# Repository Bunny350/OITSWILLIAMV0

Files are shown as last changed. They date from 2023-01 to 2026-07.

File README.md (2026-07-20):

<p align=center>
    <a>
        <picture>
  <source media="(prefers-color-scheme: dark)" srcset="https://raw.githubusercontent.com/Bunny350/OITSWILLIAMV0/master/Media/Logos/logo-whitetext.svg">
  <source media="(prefers-color-scheme: light)" srcset="https://raw.githubusercontent.com/Bunny350/OITSWILLIAMV0/master/Media/Logos/logo.svg">
  OITSWILLIAMV0
</picture>
    </a>
</p>
Project is being constantly updated. 

# OITSWILLIAMV0

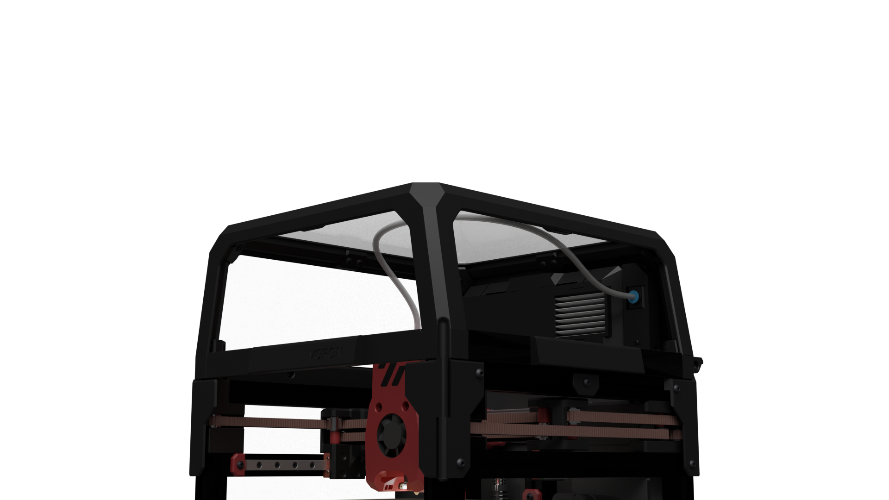
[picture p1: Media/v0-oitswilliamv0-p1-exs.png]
V0.2 + OITSWILLIAMV0 mod


Mod Repository for Voron 0.2

* Currently featured in V0.2378[^config-on-other-side]!

OITSWILLIAMV0 is a mod project for [Voron Zero](https://github.com/VoronDesign/Voron-0) 3D printer after OitswilliamV2. It comes with two different skirt themes, extended skirts and keeps some stock elements.

This mod project goes different, it is to redefine usability without making it look completely different.

## Feature development status
| Feature | Status |
| --- | --- |
| Extended skirt | Released |
| As-is top hat  | Released |
| Exhaust XS | Released |
| Back skirt with ThinkBook 14s fans | Experimental, early access |

## Extended skirt
OITSWILLIAMV0's main feature is the extended skirt, which adds additional 16mm not just to fit 40mm fans to cool down electronics. In front, left and right sides, it uses Trident skirts that are not scaled down, but cut down.

### Variant with ThinkBook 14s fans mounting
This variant is the way where we make 3D printers sound different. This replaces the original's 3510 axial fans.

## As-is top hat
OITSWILLIAMV0 also contains a mod that is used to reduce waste by keeping V0.1 top hat while adding the Cam locks that are introduced for V0.2 extrusion top hat. This mod adds 15mm spacing just for hinges, is made to not use heat seat inserts and can be printed on V0's limited build volume.

## Exhaust XS
Exhaust XS is a *different* type of exhaust unit made for Voron 0. It is intended to be different in sound and the way it is used. The filter cartridge is reusable and can be built & maintained with no tools. 

## BOM requirements and replacements

### Optional (requires extended skirt)
| Stock V0  | V0 with this mod |
| --- | --- |
| NEMA17 Stepper Motor (34mm max) with integrated lead screw 200mm T8x8 | NEMA17 Stepper Motor (40mm) with integrated lead screw 200mm T8x8* |
* Without extended skirt, this replacement will not fit.

### Additional parts

* [Exhaust XS BOM](https://docs.google.com/spreadsheets/d/1qKHTR9wy5eDcJ8kGZrhbsqijIHyDv_TbETnKIMAwmbk/edit?usp=sharing)
  
* Back skirt (legacy)
    * 1x 4010 axial fan
    * 4x M3x16mm BHCS
    * 4X M3x5x4 heat-set inserts
  
* Back skirt (with ThinkBook fans)
    * 1x ThinkBook 14s cooling fan (big)
    * 6x M2x10mm self-tapping screws

* Extended skirt legs (*dc_usb-c_sbc_exhaust_extended_skirt_middle.stl* + *dc_usb-c_sbc_exhaust_extended_skirt_top.stl*)
    * 4x M3x55mm SHCS / BHCS
    * USB-C power legging
        * 1x ThinkBook 14s cooling fan (small)
        * 3x M2x10mm self-tapping screws
        * *These are not required when using with AC power inlet skirt (power-inlet-extended-skirt.stl).*

* Rosalina Theme front covers
    * Both left and right
    * 4x M3x6mm BHCS

* Extended skirt display
    * 2x M3x12mm BHCS instead of M3x6mm BHCS
    * M3x6mm can be kept if mounting the skirt with no display.

* As-is top hat
    * 16x M2x10mm self-tapping screws
    * 8x M3x6mm BHCS

<details>
  <summary>Total BOM excluding EXS</summary>

* Total (excluding EXS)
    * 2x M3x6mm BHCS
    * 2x (without fan), 4x or 6x M3x12mm BHCS
    * 4x M3x55mm SHCS / BHCS

* Total (V0.2378 Rosalina Theme, without top hat or EXS)
    * 6x M3x6mm BHCS
    * 2x (without fan), 4x or 6x M3x12mm BHCS
    * 4x M3x55mm SHCS / BHCS

* Total (normal, with top hat, excluding EXS)
    * 16x M2x10mm self-tapping screws
    * 10x M3x6mm BHCS
    * 2x (without fan), 4x or 6x M3x12mm BHCS
    * 4x M3x55mm SHCS / BHCS

* Total (V0.2378 Rosalina Theme, with top hat, excluding EXS)
    * 16x M2x10mm self-tapping screws
    * 14x M3x6mm BHCS
    * 2x (without fan), 4x or 6x M3x12mm BHCS
    * 4x M3x55mm SHCS / BHCS
</details>

"But can you compare with the normal V0.2?" Heck yes!

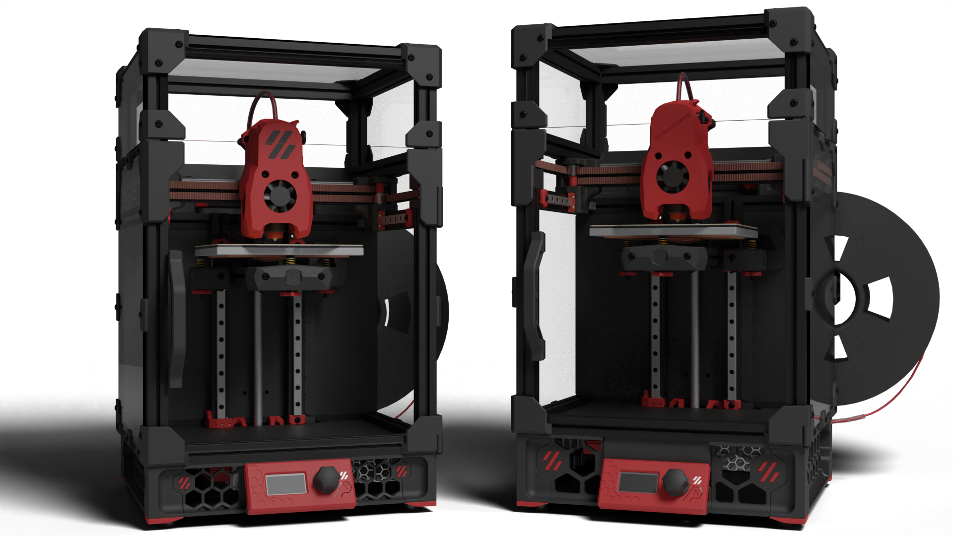
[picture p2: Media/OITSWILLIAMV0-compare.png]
Stock Voron 0.2 and Voron 0.2 with OITSWILLIAMV0 mod

As you can see, the righthand is Voron 0.2 with OITSWILLIAMV0 mod. it has the bigger Voron logo and is taller, which indicates that it uses extended skirt, which allows fit of bigger Z-axis motor. Another thing that it is different is that I modified Mini Stealthburner to reflect my mod. It is just a cosmetic mod but still Voron Mini Stealthburner.

[^config-on-other-side]: The configuration files for the following printers are not included in this repository, only organized, specific and cleaned-up. To get V0.2378's exact configuration files, you must be a follower of Oitswilliam Pang and then get follower-exclusive features through [this form](https://docs.google.com/forms/d/e/1FAIpQLSe9aEM7jyf0lV2PUAgOg0_tz9F7GI91byWFxUzvXsLlXambJA/viewform?usp=header). Other steps are provided from the form.

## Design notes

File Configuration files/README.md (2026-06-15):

# Configuration files
This folder contains mostly Klipper configuration files.

## Guide
* fn_key.cfg
    * A configuration file made specifically to replace *kill_switch* inside *[display]* section. If the key in-question has wired directly to the reset key of MCU then this will be useless.
    * Default functions are provided.
* exs.cfg
    * A dedicated configuration file made for Exhaust XS.

## Other notes
* Only followers of Oitswilliam Pang from Facebook, Instagram and subscribers on YouTube can view and borrow Oitswilliam's printers' (V0.2378) current configurations. This folder holds cleaned-up configurations.

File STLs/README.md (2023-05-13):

This folder stores STLS of this project.
## Compatibility
All mods contained in this project only support Voron Zero 3D printer and some may support 3D printers that use 1515 extrusion as frames.

## Color guide
* [acc] - Printer accent color.
* [base] - Printer base color.
* [transparent] - Transparent color, it should allow the glow to pass-through and can be diffused. Transparent PETG is recommended.
* [rc] - Rosalina Cyan; the best matching color for Oitswilliam's is Polymaker PolyLite ABS teal. This only occur in Rosalina-theme parts.
* If the part name does not have any brackets at the beginning you can use the printer's base color or better use the least used filament to print the part. These parts are mostly hidden on the outside.

##  Printing guidelines
This section tells how to basically configure print settings.
Some parts require a bigger printer to print.
### Settings
These parts require ABS or PETG to print.
Settings and parameters must be set to the following values:
* Layer height 0.2mm
* Layer width of 1.6mm or 4 layer lines
* Infill density of 40%, but,
    * On LED diffusers ([transparent]led-diffuser), the recommended infill density is 100%,
* Any slicers are welcome.
* Some inner parts such as grills requires modifiers to optimize printing performance.

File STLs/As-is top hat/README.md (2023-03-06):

This folder contains essential components of As-is top hat mod.

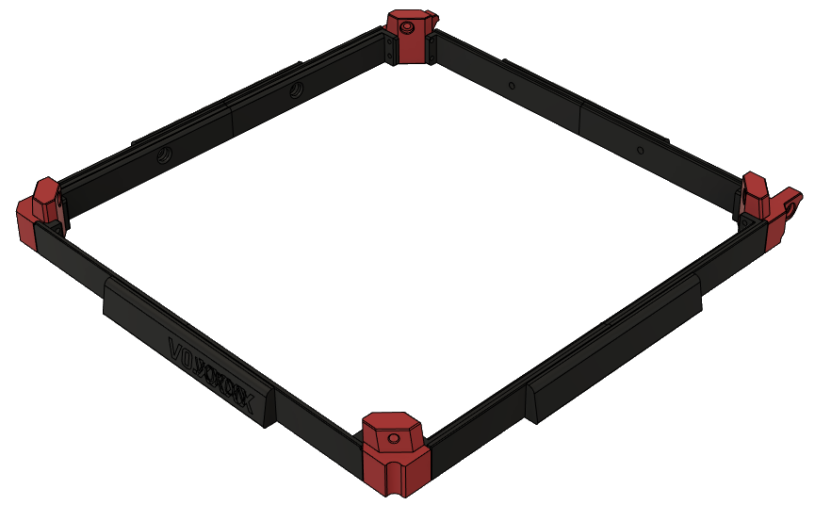
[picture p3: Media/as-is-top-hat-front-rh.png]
As-is top hat mod front-right

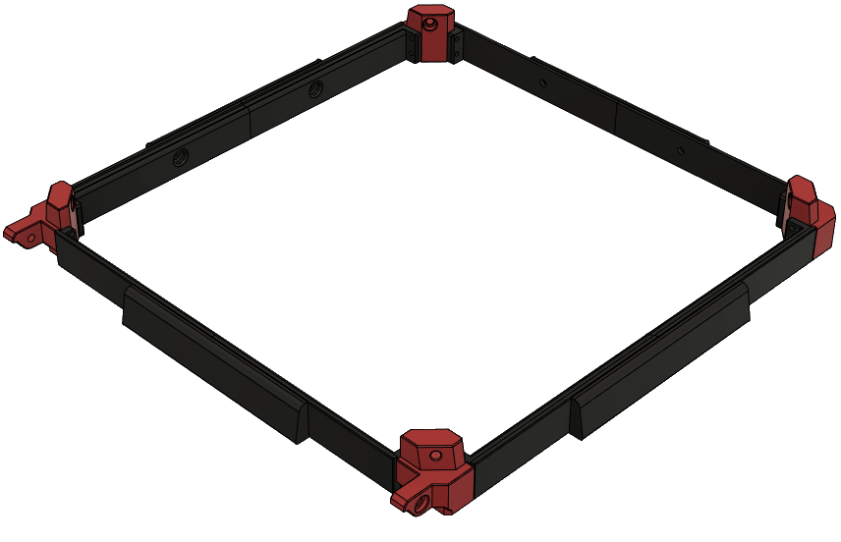
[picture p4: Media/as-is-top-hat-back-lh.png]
As-is top hat mod back-left


## Printing guide

You may print all the parts in this folder, but not this folder's subfolders, in which you may print either one of the versions of side panels, normal, thick or ultra-thick.

### Side panels foam taping
There are requirements in which the thickness the foam tape is needed.
* Thick version requires at least 3mm thick foam tapes.
* Ultra-thick version does not require any foam tapes in the side. It is optional.

## Assembling As-is top hat

Oitswilliam Pang made a simple design that makes the top hat mod assembly easy, these mount covers are directional, and they need to be faced. Front and back has mount offsets, while the side spacing brackets are thicker.

Re-printing V0.1 top hat is not required, if you have one that isn't been disassembled or salvaged.

Before attaching the corners, they need to be assembled as a ring or halo.

If you want the cam lock feature with this mod, you can attach M3x10mm screws to the bottom hole of the front corners. In V0.2 assembly guide page 232, the screws needs to be spaced and is fixed at 5mm.

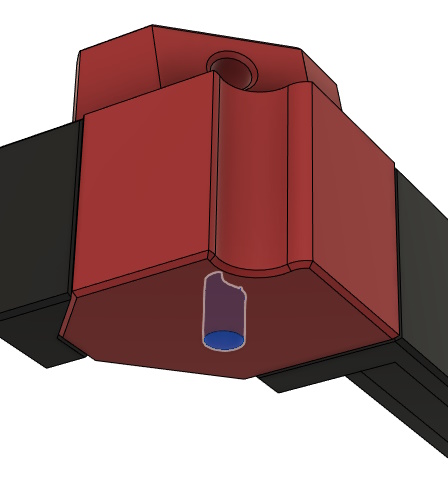
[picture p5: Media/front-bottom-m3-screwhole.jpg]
M3x10mm Cam lock mounting screw hole in one of the corners


To assemble the ring or halo, you attach the spacing brackets to the corners, and secure it with 2 M2x10mm self-tapping screws on each corner, or 4 on each side / corners (16 total). 

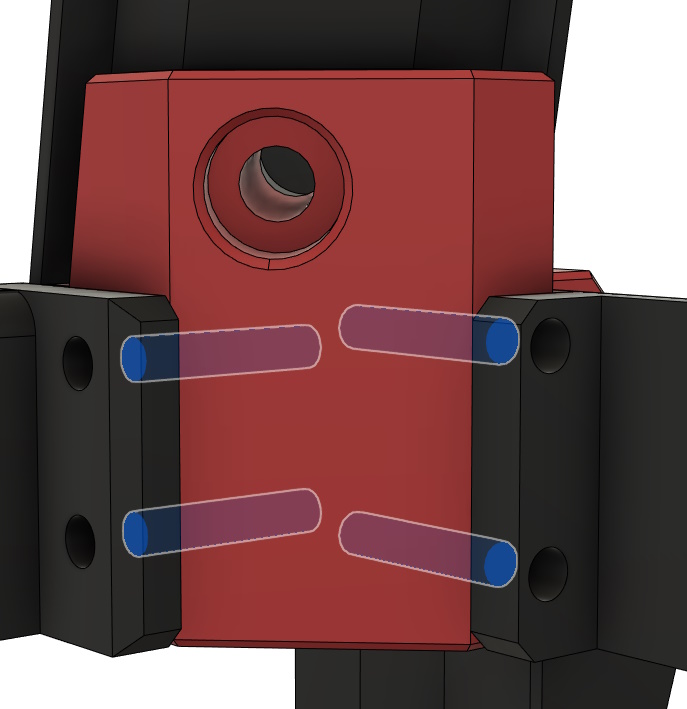
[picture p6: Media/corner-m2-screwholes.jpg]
Mounting holes for attaching M2x10mm self-tapping screws to one of the corners


Then you combine the spacing brackets first, by mounting them with *spacer-holder*, and secure with 2 M3x6mm screws per side (8 total).

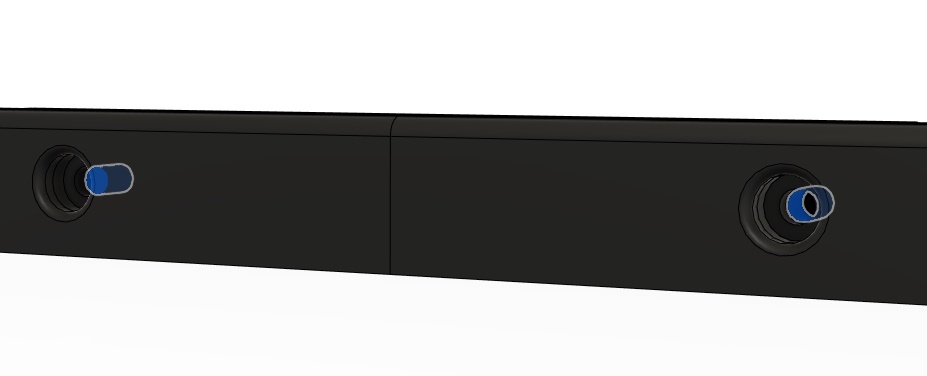
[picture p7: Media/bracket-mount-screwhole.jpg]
M3x6mm to spacer-holder screw mount holes


This is then you can attach the ring or halo assembly that has corners with M3x12 screws in V0.1 assembly manual, and you may follow the rest in V0.2 assembly manual, most specifically back to page 238.

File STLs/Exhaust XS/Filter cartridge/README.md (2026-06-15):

## Known issues
* In some cases Klipper has an issue where it causes an error on moves out of range. Especially on V0 printers with input shaping tuned and enabled.
    * This is not the slicer-side issue, but rather the printer-side issue.
    * To address this, off-center exs_v0_filter_cartridge_carbon_pellet.stl slightly left around 0.4mm in the slicer.

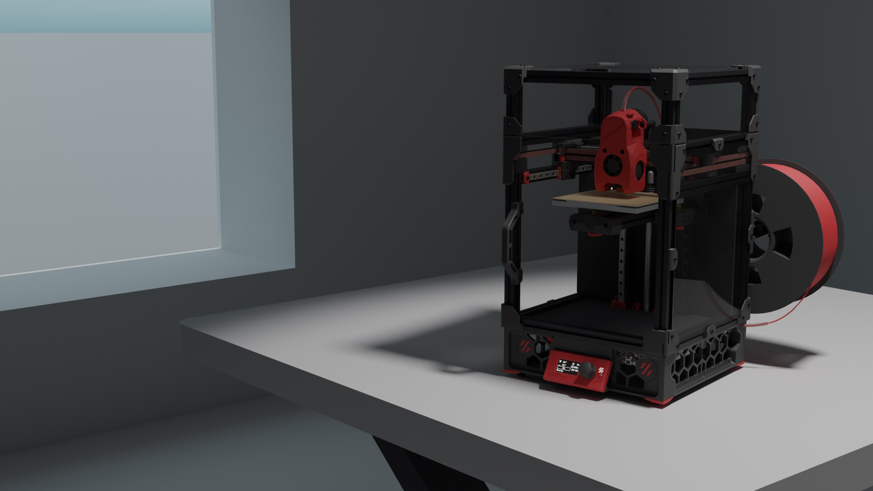
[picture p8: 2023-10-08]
Media/v0-oitswilliamv0-p1-finale.jpg

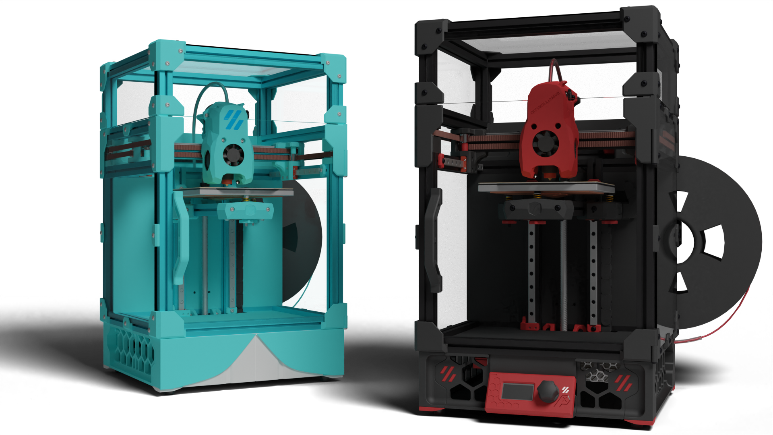
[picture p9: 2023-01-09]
Media/Past renders/OITSWILLIAMV0.png

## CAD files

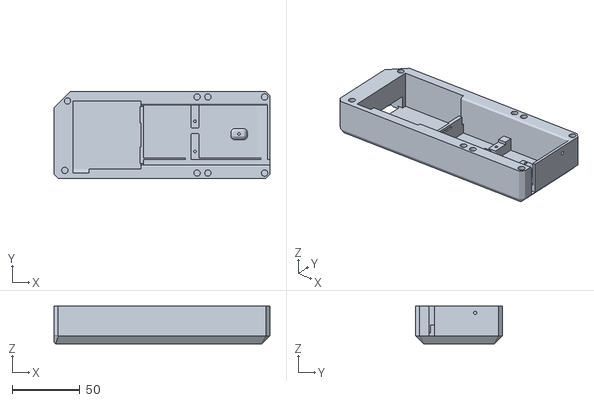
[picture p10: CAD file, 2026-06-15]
STLs/Exhaust XS/Filter mount/Main full/exs_v0_filter_main_unit_bottom.stl
160.0 x 64.4 x 28.0

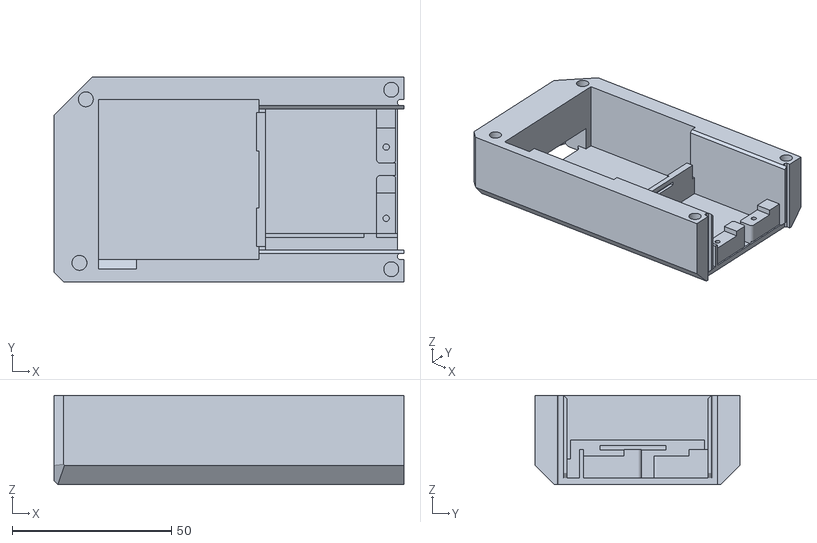
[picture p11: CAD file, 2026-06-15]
STLs/Exhaust XS/Filter mount/Main splitted/exs_v0_filter_main_unit_bottom_split_l.stl
110.0 x 64.4 x 28.0

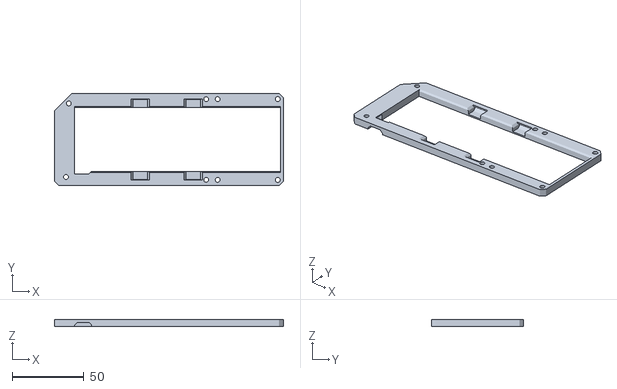
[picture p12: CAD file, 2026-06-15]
STLs/Exhaust XS/Filter mount/Main full/exs_v0_filter_main_unit_top.stl
160.0 x 64.4 x 5.00

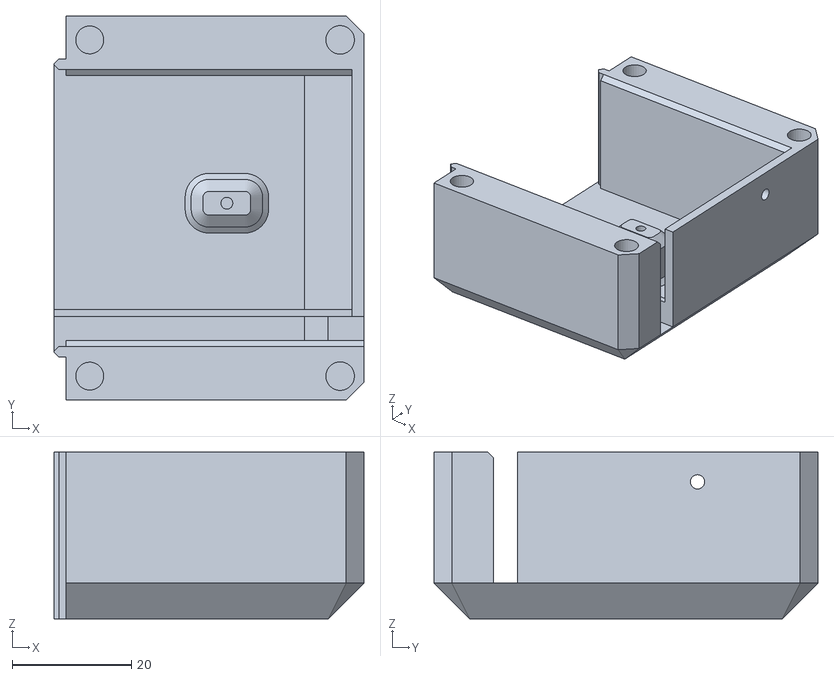
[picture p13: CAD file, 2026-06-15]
STLs/Exhaust XS/Filter mount/Main splitted/exs_v0_filter_main_unit_bottom_split_r.stl
52.0 x 64.4 x 28.0

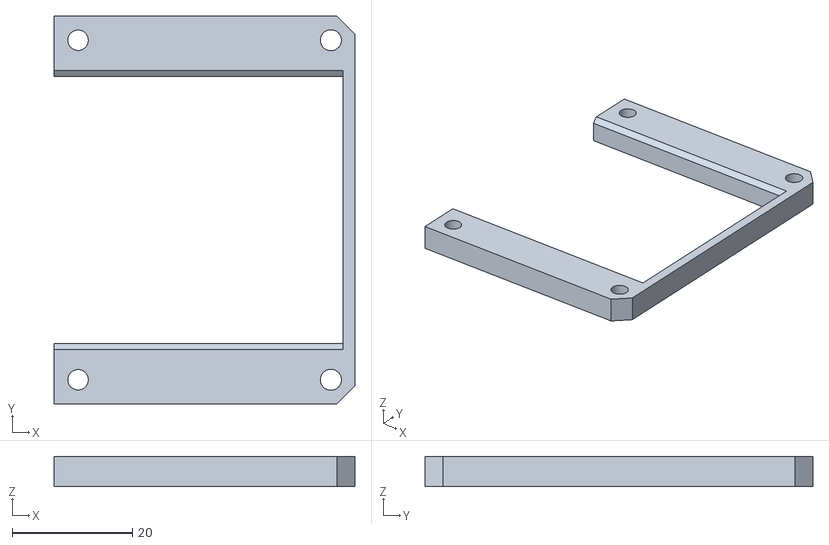
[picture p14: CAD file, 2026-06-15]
STLs/Exhaust XS/Filter mount/Main splitted/exs_v0_filter_main_unit_top_split_r.stl
50.0 x 64.4 x 5.00

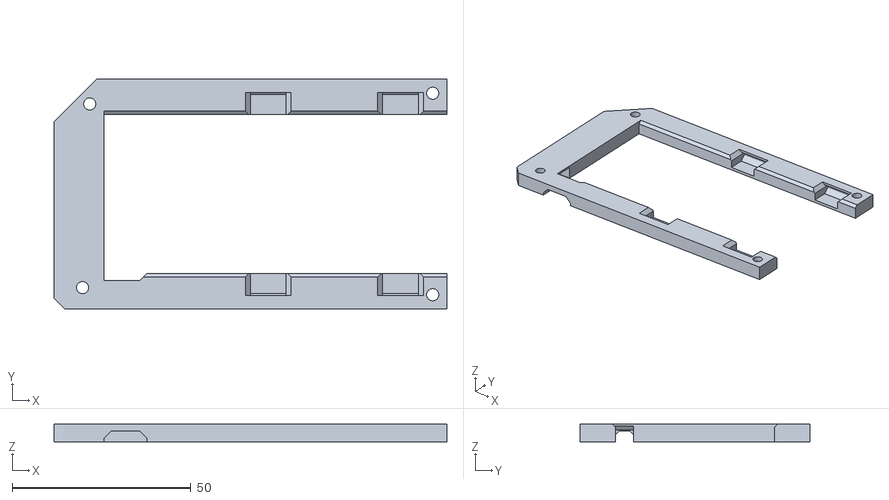
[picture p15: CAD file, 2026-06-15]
STLs/Exhaust XS/Filter mount/Main splitted/exs_v0_filter_main_unit_top_split_l.stl
110.0 x 64.4 x 5.00

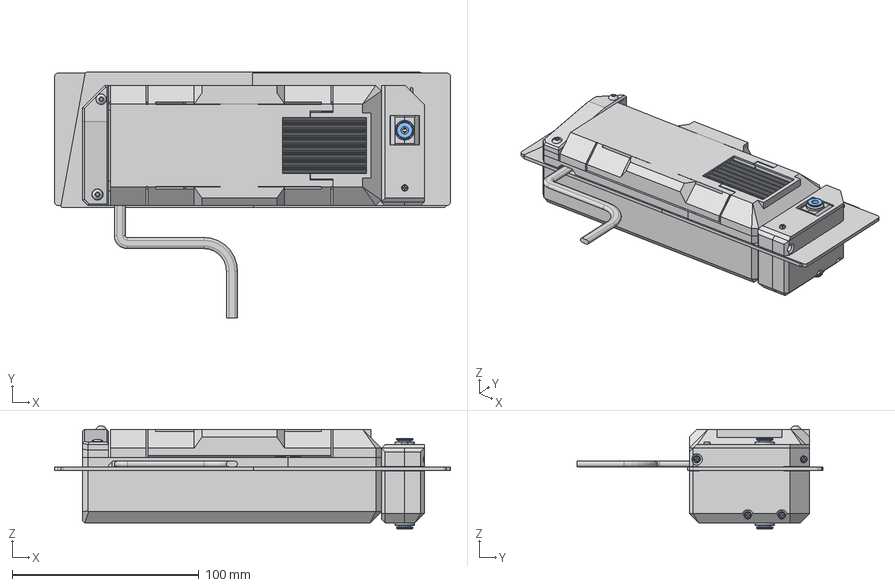
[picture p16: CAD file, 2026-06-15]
CAD/Exhaust XS/EXS for voron 0.step
212.0 x 131.4 x 54.9 mm
[raw] hepa filters
filter cartridge
99461A917_NO THREADS_Phillips Rounded Head Thread-Forming Screws x 13
KW10 Microswitch (2)
10x20x0.7 stainless steel spring - compressed
Omron D2F Microswitch
4mm OD 2mm ID PTFE tube
MR85 Bearing x 2
led mount
[raw]babydrone back led
v0.1 panel
v0.2 panel
main unit splitted
92095A182_NO THREADS_Button Head Hex Drive Screw x 8
ISO 7380-1 - M3 x 30 Steel 4.6 Plain
ISO 7380-1 - M3 x 30 Steel 4.6 Plain_1
M3 Threaded Insert x 8
ECAS04 Bowden Collet x 2
raw - 5010 blower fan
raw - cabling - for reference only
raw - foam tape

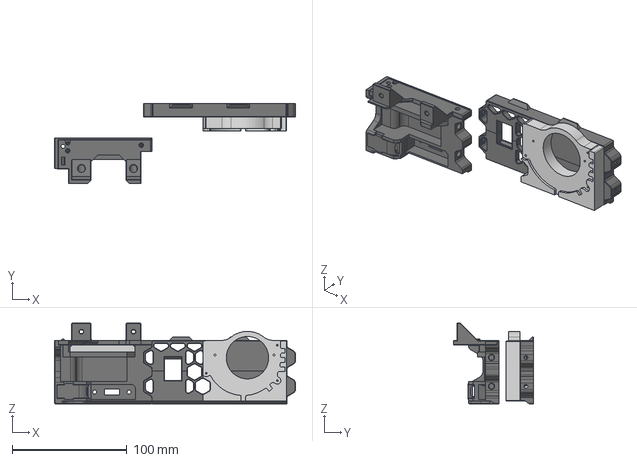
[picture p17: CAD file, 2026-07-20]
CAD/Experimental/voron 0 skirt with laptop fan mod.step
210.5 x 70.0 x 70.5 mm

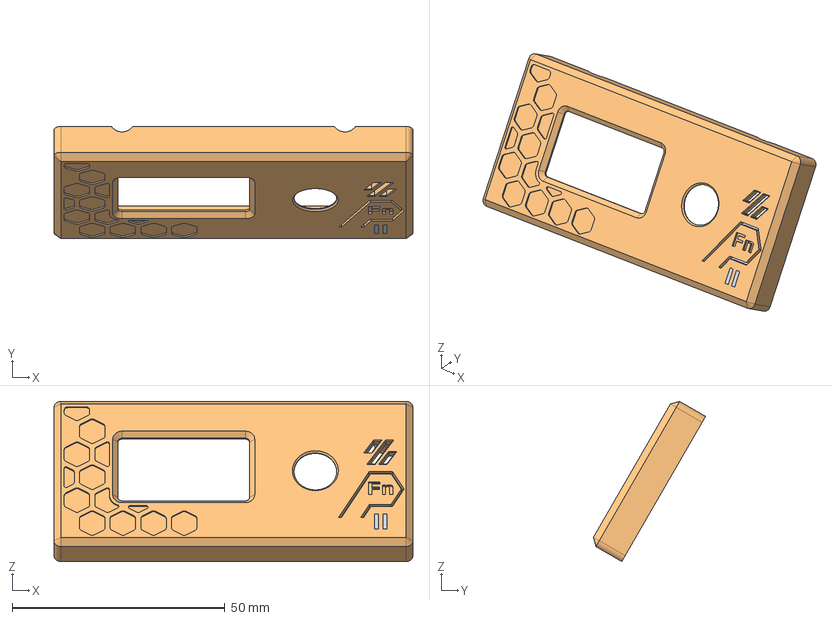
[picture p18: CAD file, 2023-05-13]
CAD/Faceplates with Function key/voron 0.2 display front faceplate with fn button v2.step
84.4 x 26.4 x 37.6 mm

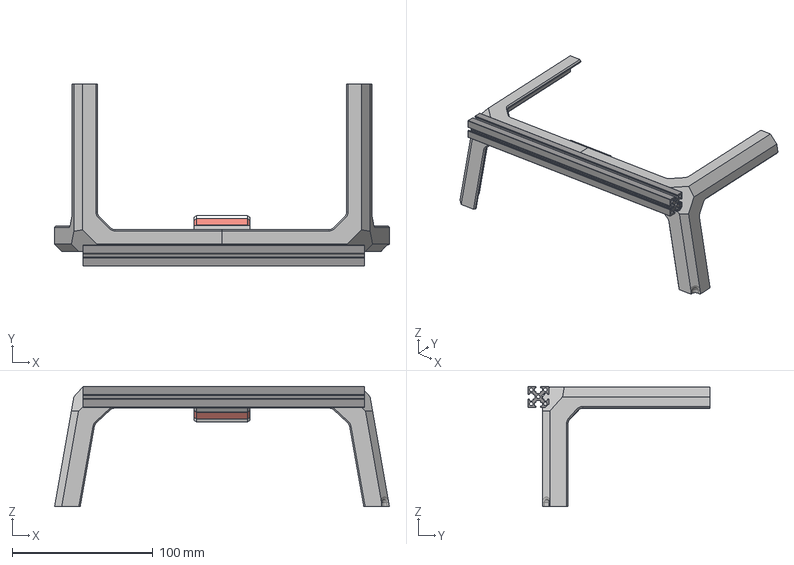
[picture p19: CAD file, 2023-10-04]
CAD/Top hat LED/v0 led addon v4.step
238.0 x 129.6 x 85.5 mm
M3x8 BHCS-1 x 3
original parts
M3 Hexnut
original parts (1)
frame side magnet
M2x10 Self-tapping Screw (2) x 4
WS2812B LED v1 x 2
led side magnet
wire

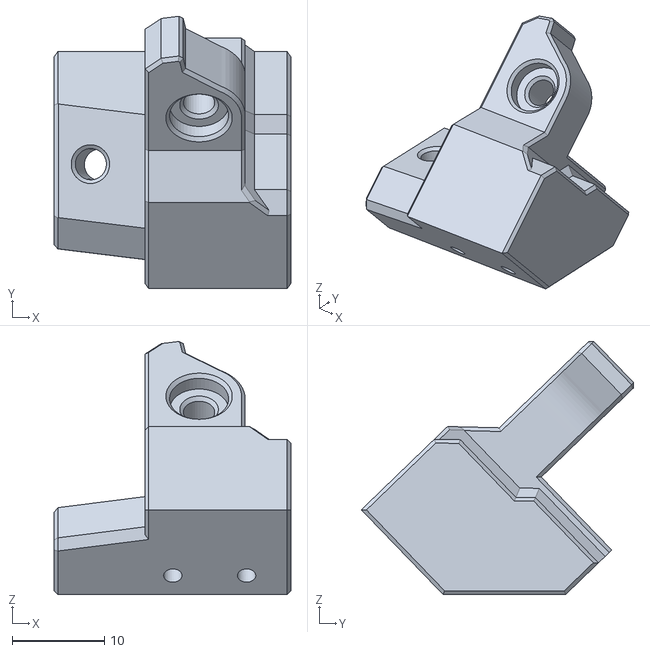
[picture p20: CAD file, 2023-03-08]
STLs/As-is top hat/corner-hinge-left.stl
25.6 x 29.5 x 27.4

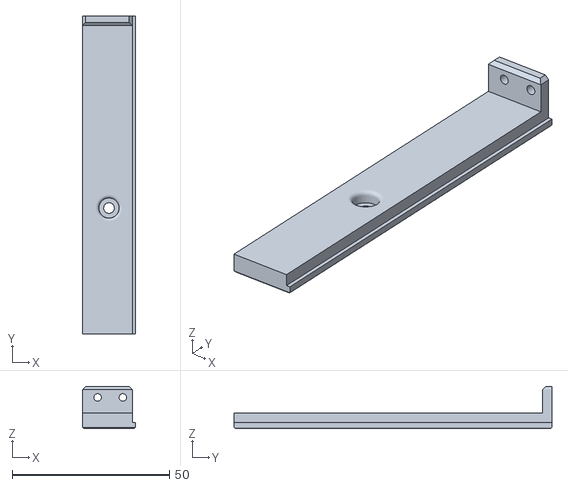
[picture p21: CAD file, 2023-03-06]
STLs/As-is top hat/Thick/spacer-side-thick-mirror-X2.stl
16.8 x 101.0 x 13.4

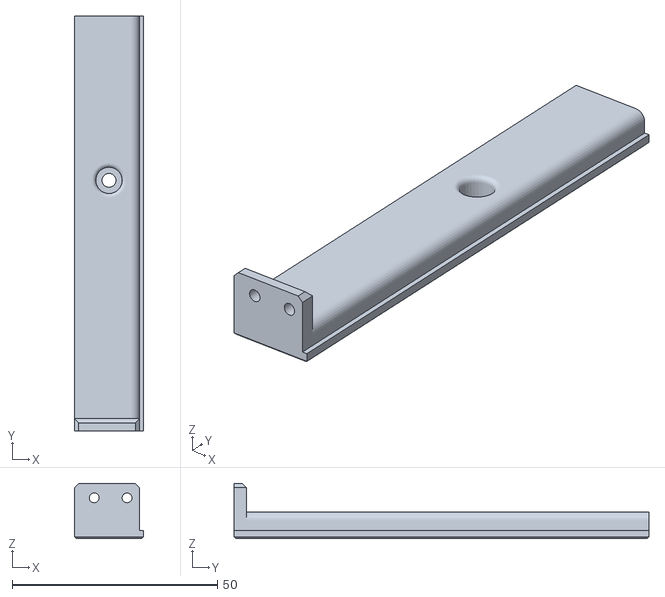
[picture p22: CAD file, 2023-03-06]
STLs/As-is top hat/Ultra-thick/spacer-side-ultra-thick-X2.stl
16.8 x 101.0 x 13.4

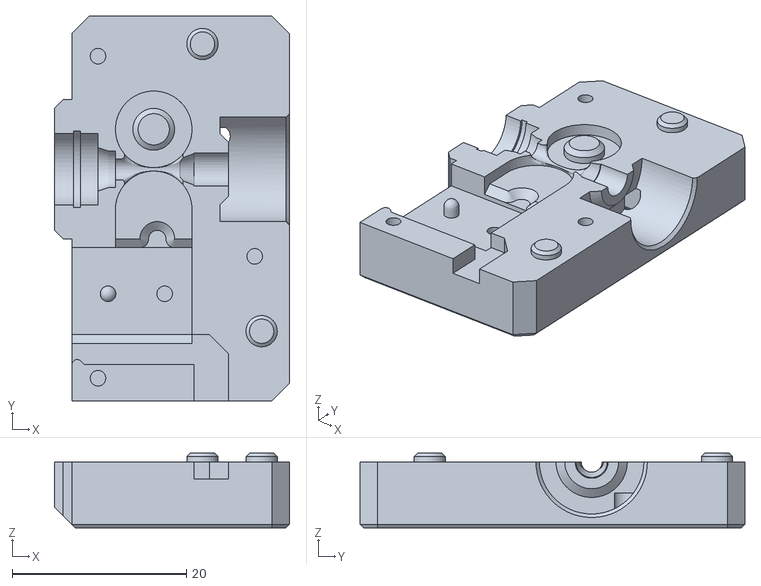
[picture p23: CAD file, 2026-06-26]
STLs/Exhaust XS/Filament sensor/exs_presence_tangle_pres_l.stl
27.0 x 44.2 x 8.60

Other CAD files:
STLs/Exhaust XS/Filter cartridge/exs_v0_filter_cartridge_front_bracket.stl
STLs/Exhaust XS/Filter mount/exs_v0_filter_reserved.stl
STLs/Exhaust XS/LED unit/exs_led_unit_shell.stl
STLs/Exhaust XS/Unit panel mount/V0.1 (printed top-hat)/filter_mount_panel_v0-1_l.stl
CAD/Exhaust XS/EXS for voron 0.f3d
CAD/Experimental/voron 0 skirt with laptop fan mod.f3d
CAD/Faceplates with Function key/voron 0.2 display front faceplate with fn button v2.f3d
CAD/Rest of assembly/OITSWILIAMV0 P1 V0.2.f3d
CAD/Top hat LED/v0 led addon v4.f3d
STLs/As-is top hat/Thick/spacer-side-thick-X2.stl
STLs/As-is top hat/Ultra-thick/spacer-side-ultra-thick-mirror-X2.stl
STLs/As-is top hat/corner-front-left.stl
STLs/As-is top hat/corner-front-right.stl
STLs/As-is top hat/corner-hinge-right.stl
STLs/As-is top hat/spacer-front-lefthand.stl
STLs/As-is top hat/spacer-front-righthand.stl
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

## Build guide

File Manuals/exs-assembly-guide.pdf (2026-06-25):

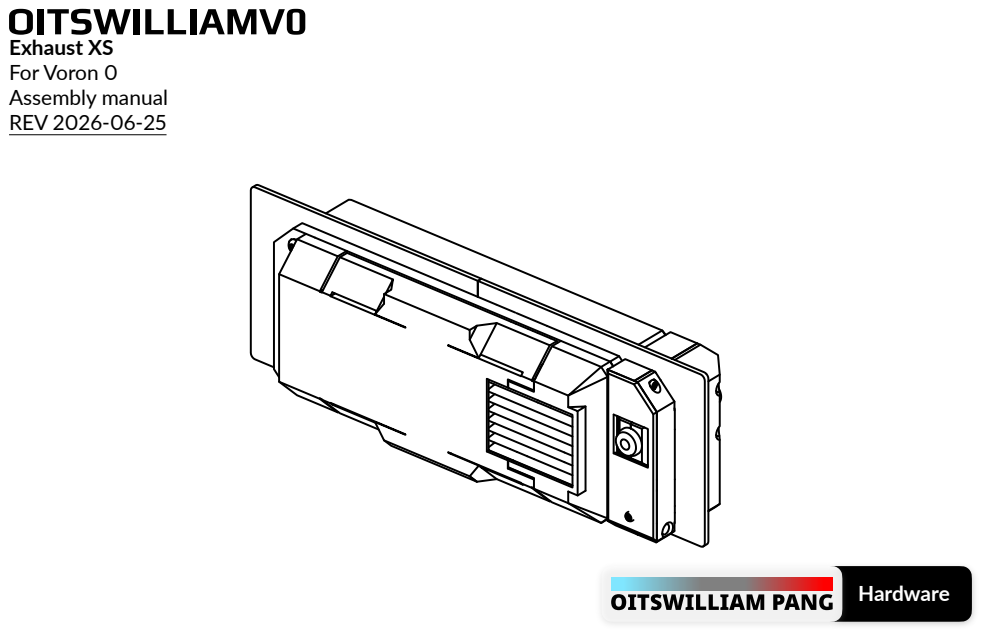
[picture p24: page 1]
Exhaust XS For Voron 0 Assembly manual REV 2026-06-25; Hardware

2
Contents • Before getting started • Assembly • Filter cartridge • Hybrid filament sensor • The outer side • LED unit • Crafting • Attaching and removal • Software configuration • Troubleshooting

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
# Before getting started

You are about to read the manual of Exhaust XS.
Warning
Danger: unless if it only runs on DC and only has a DC input, otherwise risk of electric shock
- Even though you can build with this mod from start, if you want to wire, or re-wire, you need to make sure and check that the mains is unplugged.
- Failure doing so which is unplugging the mains power may cause electrocution or even death.
- When in doubt, please don't touch the wires connected to the power supply or SSR.
Other notes
- Exhaust XS does not support hose adapters from ELG2 or ELG1.
- There is a reserved component that is [redacted], but we will reveal it within foreseeable future, so stay tuned (https://www.oitswilliam.com/media) by following Oitswilliam Pang in Facebook, Instagram and YouTube.

About Exhaust XS
Exhaust XS (XS stands for eXtra small, abbreviated EXS) is Oitswilliam-designed exhaust unit made for Voron 0. It is low-profile, has dual-layer HEPA filters to filtrate microplastics and activated carbon pellets to capture VOCs. EXS uses 5010 blower fan to make exhausting sound different whilst performant. It partially uses Voron Design's Stealth design scheme. EXS uses compliant design just to reduce raw materials and ease assembly, such as removable pellet panel and tool-less cartridge removal. It will pave for the next generation of EL for standard Voron printers.

Dark lore: The name EXS has been around inside Oitswilliam's brain since around 2024.

4
Compatibility
Exhaust XS is compatible with Voron 0, with pre-made 3D-printable panels made specifically for V0.1 (printed top-hat) and V0.2 (extrusion top-hat). Other printers that are smaller than 40cm in either dimensions and did not have a pre-done exhaust cutout are also applicable. Note that top-hat from Voron 0.0 is incompatible.

Contribution
This project can be contributed through GitHub. You can visit, contribute and report new issues here. (https://github.com/Bunny350/alpha-ea/) Technical support
You can contact Oitswilliam here. (http://oitswilliam.com/support) You can email or direct message Oitswilliam in Facebook. Or if the issue is not related to OITSWILLIAMV0 mod, but rather most of Voron parts, you may visit Voron forum or its Discord server.

Guide and legend

- - raw material
- - highlighted material
- - printed material, as this part is simple, the printed parts may be color-coded.

Material

Model
model.stl / model.3mf

Material

5
Part printing
The parts of this model can be printed in the base color of the printer. Bold text indicates the recommended value and italic text indicates on what setting / value it needs to set. Diffuser part require transparent materials, commonly seen in PETG or PC.

Additional maker tools
To get started building the project, you may use the following tools:
- Wire crimping tool - to make custom-length connectors,
- Soldering iron - to connect the switches with wires,
- Heat shrink tubings, in 2mm diameter, three colors minimum.
FDM / FFF or SLS | Print material: ABS, ASA or PA12, prohibits PLA.
Layer height of 0.2mm, initial layer height can be 0.2mm or higher. | Nozzle and extrusion width must be forced 0.4mm; if using 0.4mm nozzle
1.6mm wall width, or 4 wall counts. | Infill must be at least 40%, except on the infill modifiers.
At least 4 solid bottom and top layers, except on the infill modifiers. | The best print speed is up to 120mm/s. The speed might be reduced by the hot end flow rate.
Supports are recommended for main skirt parts. Use tree or organic supports if available. | Other settings might be depended on your printer. Follow it's warnings for proper handling.

# Assembly

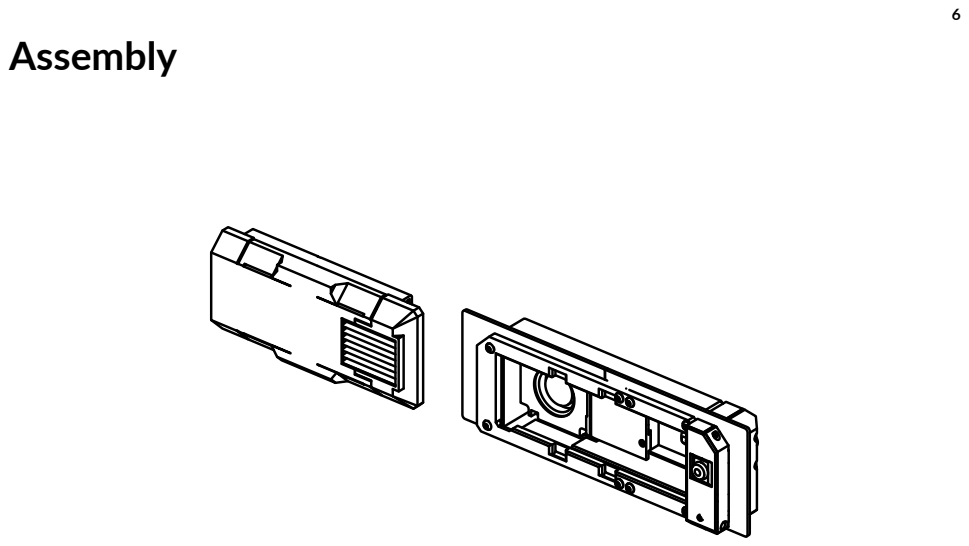
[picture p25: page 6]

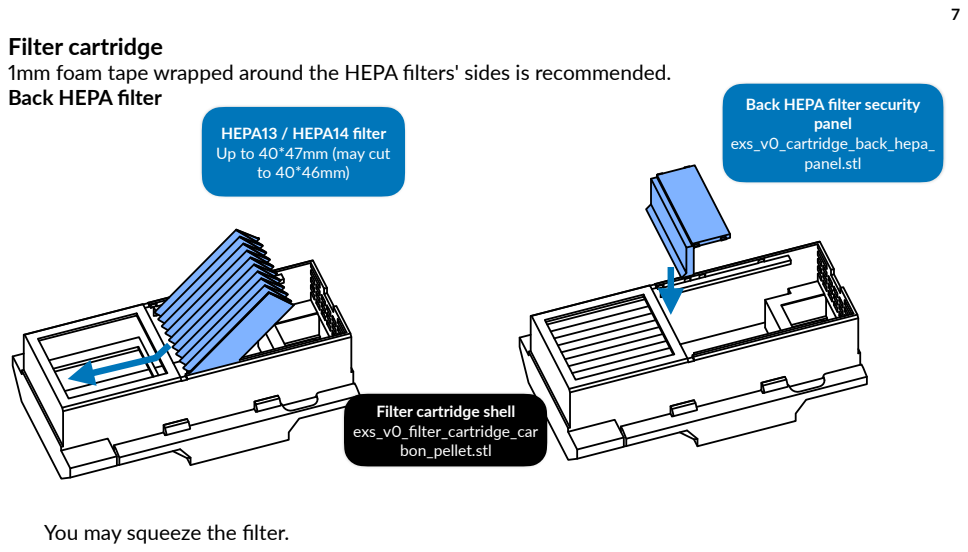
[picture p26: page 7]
Filter cartridge shell exs_v0_filter_cartridge_car bon_pellet.stl; panel exs_v0_cartridge_back_hepa_ panel.stl

Filter cartridge
1mm foam tape wrapped around the HEPA filters' sides is recommended.
Back HEPA filter

Back HEPA filter security

HEPA13 / HEPA14 filter
Up to 40*47mm (may cut

You may squeeze the filter.

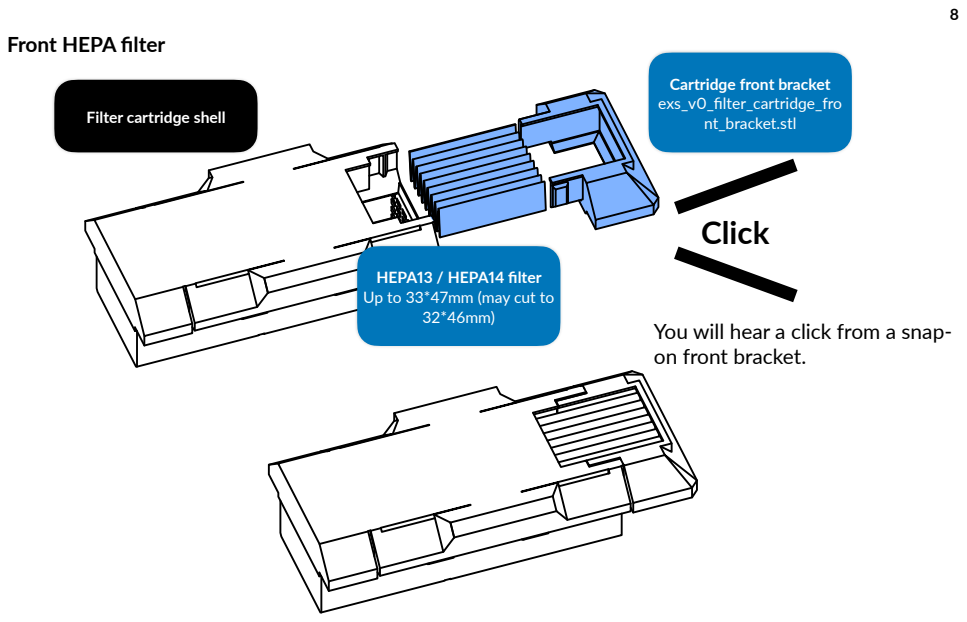
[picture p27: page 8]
Cartridge front bracket exs_v0_filter_cartridge_fro nt_bracket.stl; Click

Front HEPA filter

Filter cartridge shell

HEPA13 / HEPA14 filter
Up to 33*47mm (may cut to

You will hear a click from a snap-
on front bracket.

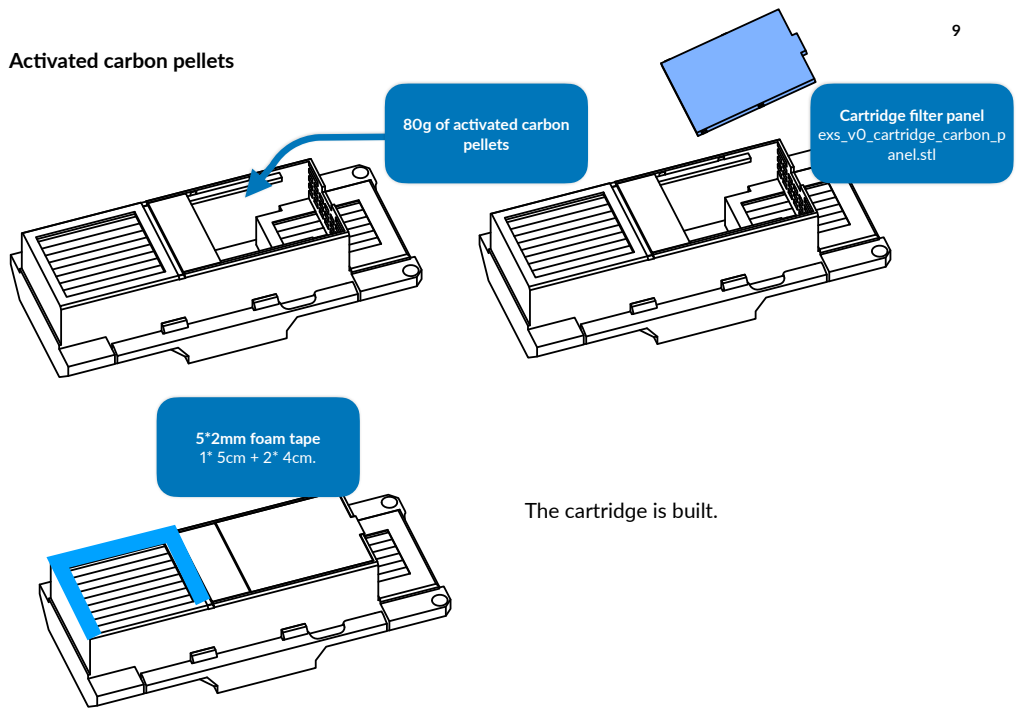
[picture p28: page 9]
pellets; anel.stl; 5*2mm foam tape 1* 5cm + 2* 4cm.

Activated carbon pellets

Cartridge filter panel
exs_v0_cartridge_carbon_p

80g of activated carbon

The cartridge is built.

10
Hybrid filament sensor (presence and tangle sensor)
This is recommended if your Voron 0 did not have any filament run-out and / or tangle sensor. EXS can be installed with or without hybrid filament sensor. This can be ignored if you are installing EXS with Mellow MDM.
Wiring

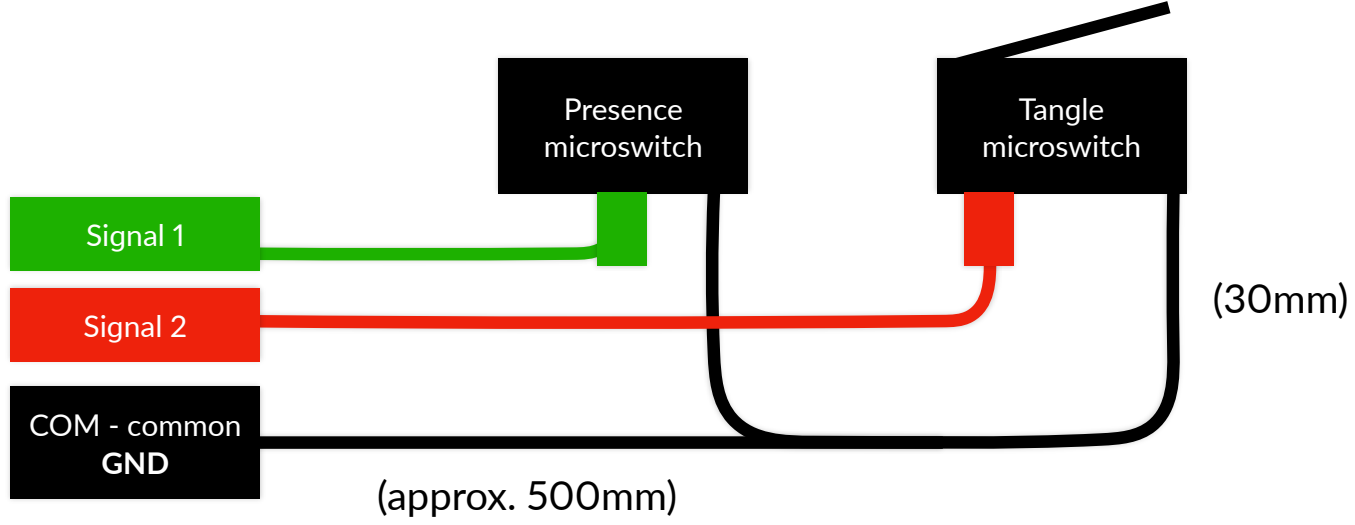
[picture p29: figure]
Presence microswitch; Tangle microswitch; COM - common GND; Signal 1; Signal 2; (approx. 500mm)

Note: it's best time to have two pairs & three colors of heat-shrink tubes for color indication.
Connect the first long signal wire to the normally open (NO) terminal of the presence switch, and then connect the second long signal to the normally closed (NC) terminal of the tangle switch, after that, use the 30mm wire to connect the common (COM) of the switches and use the last long signal wire to the presence switch.

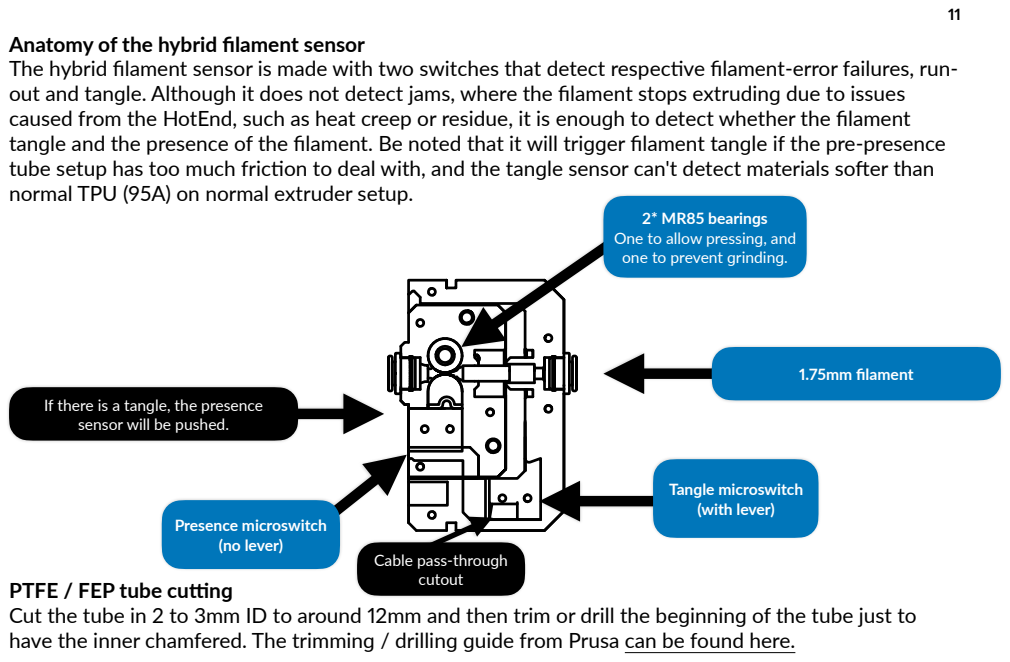
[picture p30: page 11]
1.75mm filament; Presence microswitch (no lever); Tangle microswitch (with lever)

Anatomy of the hybrid filament sensor
The hybrid filament sensor is made with two switches that detect respective filament-error failures, run-
out and tangle. Although it does not detect jams, where the filament stops extruding due to issues
caused from the HotEnd, such as heat creep or residue, it is enough to detect whether the filament
tangle and the presence of the filament. Be noted that it will trigger filament tangle if the pre-presence
tube setup has too much friction to deal with, and the tangle sensor can't detect materials softer than
normal TPU (95A) on normal extruder setup.

2* MR85 bearings
One to allow pressing, and
one to prevent grinding.

If there is a tangle, the presence
sensor will be pushed.

Cable pass-through
cutout

PTFE / FEP tube cutting
Cut the tube in 2 to 3mm ID to around 12mm and then trim or drill the beginning of the tube just to
have the inner chamfered. The trimming / drilling guide from Prusa can be found here. (https://help.prusa3d.com/guide/how-to-trim-ptfe-tube-original-prusa-printers_22424)

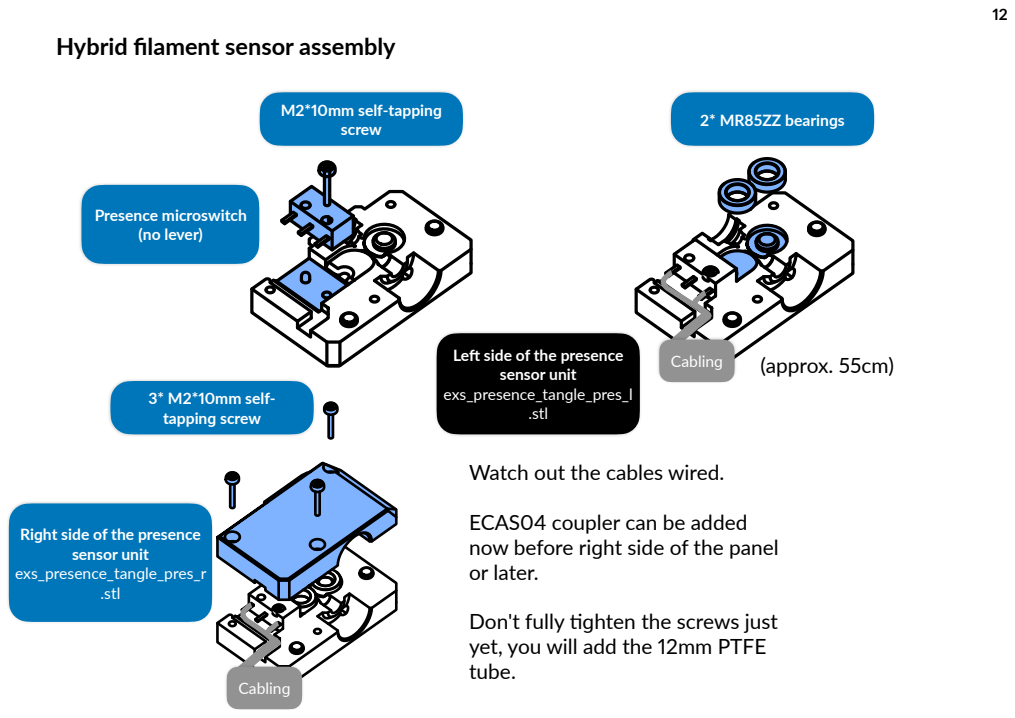
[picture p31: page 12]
Presence microswitch (no lever); M2*10mm self-tapping screw; .stl; 2* MR85ZZ bearings; exs_presence_tangle_pres_r .stl; 3* M2*10mm self- tapping screw; Cabling; (approx. 55cm)

Hybrid filament sensor assembly

Left side of the presence
sensor unit
exs_presence_tangle_pres_l

Watch out the cables wired.

ECAS04 coupler can be added
now before right side of the panel
or later.

Right side of the presence

Don't fully tighten the screws just
yet, you will add the 12mm PTFE
tube.

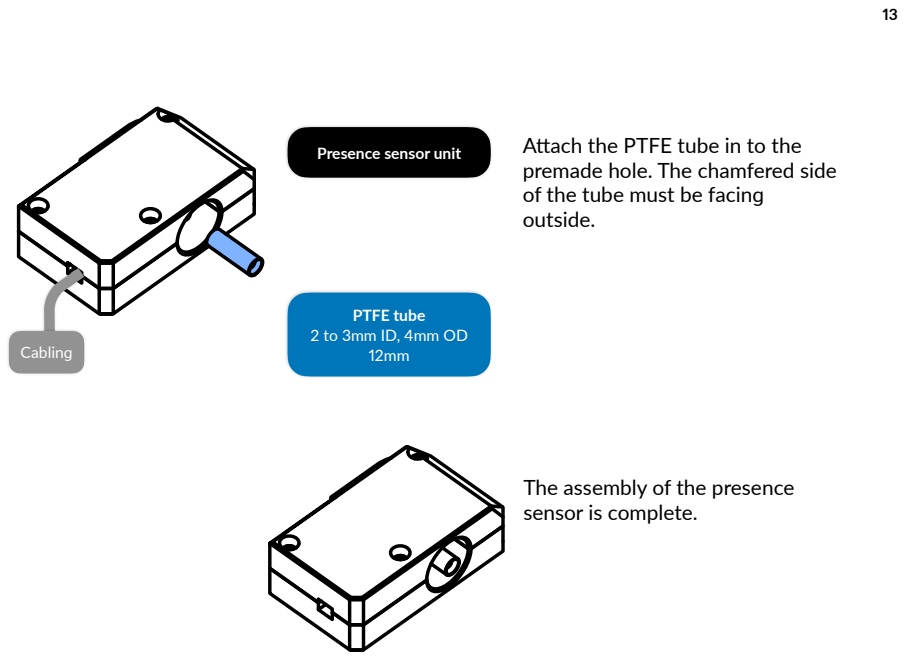
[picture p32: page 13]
Cabling

Attach the PTFE tube in to the
premade hole. The chamfered side
of the tube must be facing
outside.

Presence sensor unit

PTFE tube

The assembly of the presence
sensor is complete.

14
Tangle sensor

Presence sensor unit

M2*10mm self-tapping
screw

10*25*0.7mm stainless
steel spring

Note: watch out for the cables. You may lift the presence sensor up. Note: you may pass the wires through the cutout near the
tangle switch mount.
Test the tangle microswitch by pressing the presence sensor and the shell, you may put the hand at the righthand side of the presence sensor as to prevent component flyaway.
You should hear a click, if not, the switch might be incompatible or the part printed has settings badly tuned. If the problem persists, please flag it as error on GitHub.com/Bunny350/OITSWILLIAMV0/issues.

Left side of the sensor
unit shell
exs_presence_tangle_sh
ell_l.stl

(Cabling approx.
55cm)

Tangle microswitch (with
lever)

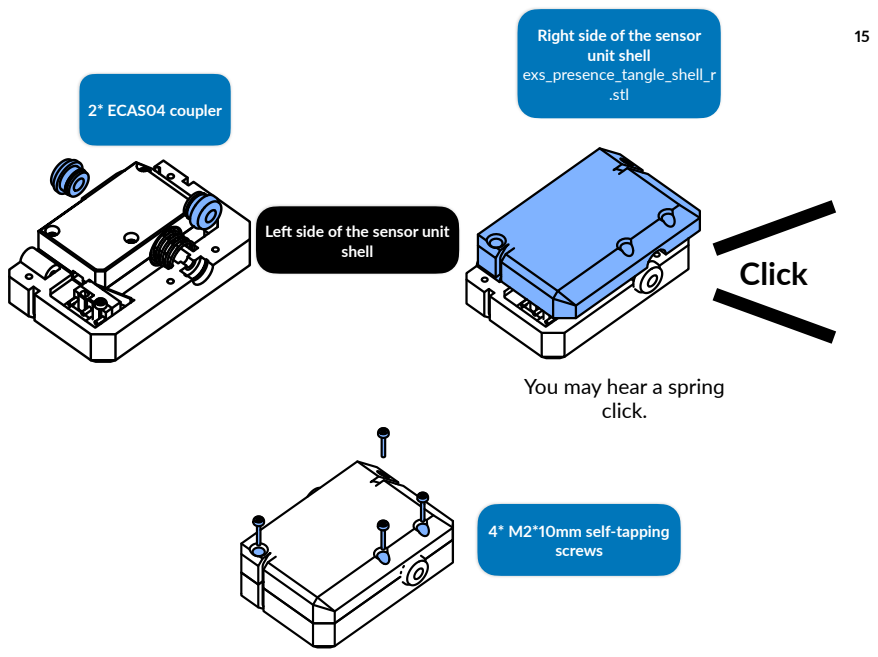
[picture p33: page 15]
Right side of the sensor; unit shell exs_presence_tangle_shell_r .stl; shell; 2* ECAS04 coupler; Click; 4* M2*10mm self-tapping screws; click.

Left side of the sensor unit

You may hear a spring

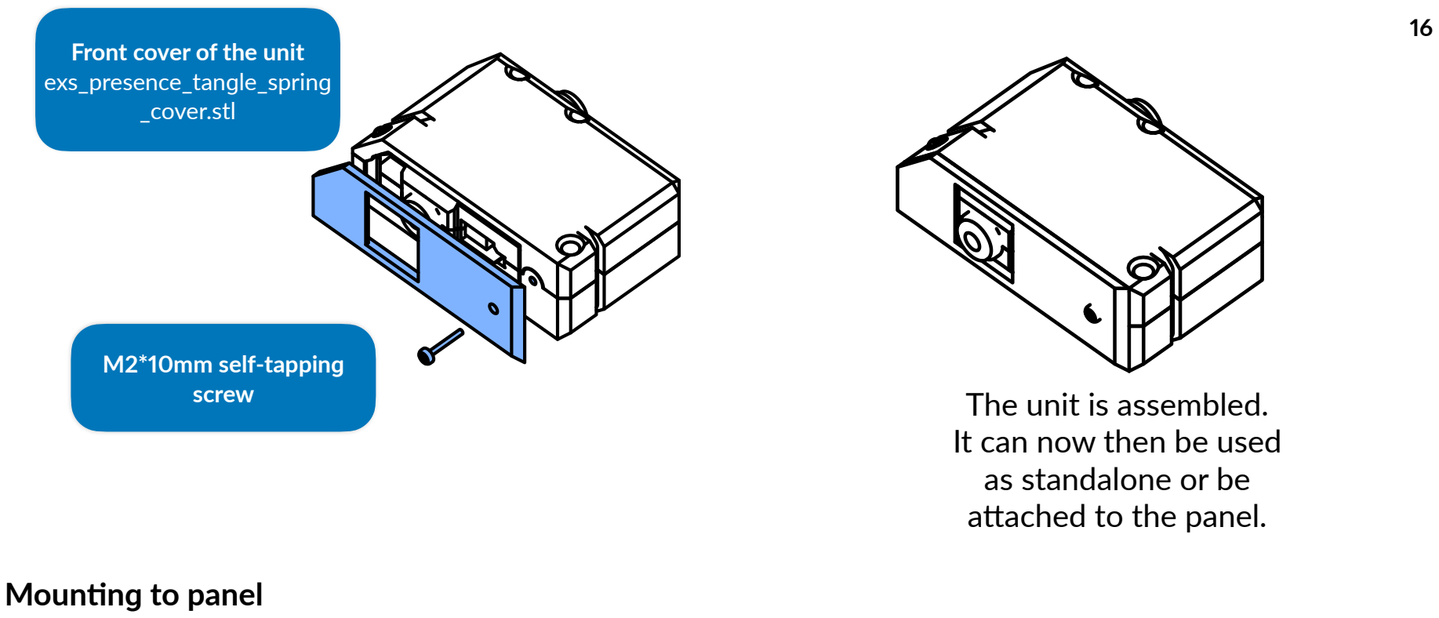
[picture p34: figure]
Mounting to panel; Front cover of the unit exs_presence_tangle_spring _cover.stl; M2*10mm self-tapping; screw; The unit is assembled.; It can now then be used as standalone or be attached to the panel.

Showing panel mount for extrusion top-hat. This instruction is compatible with variants for printed top-

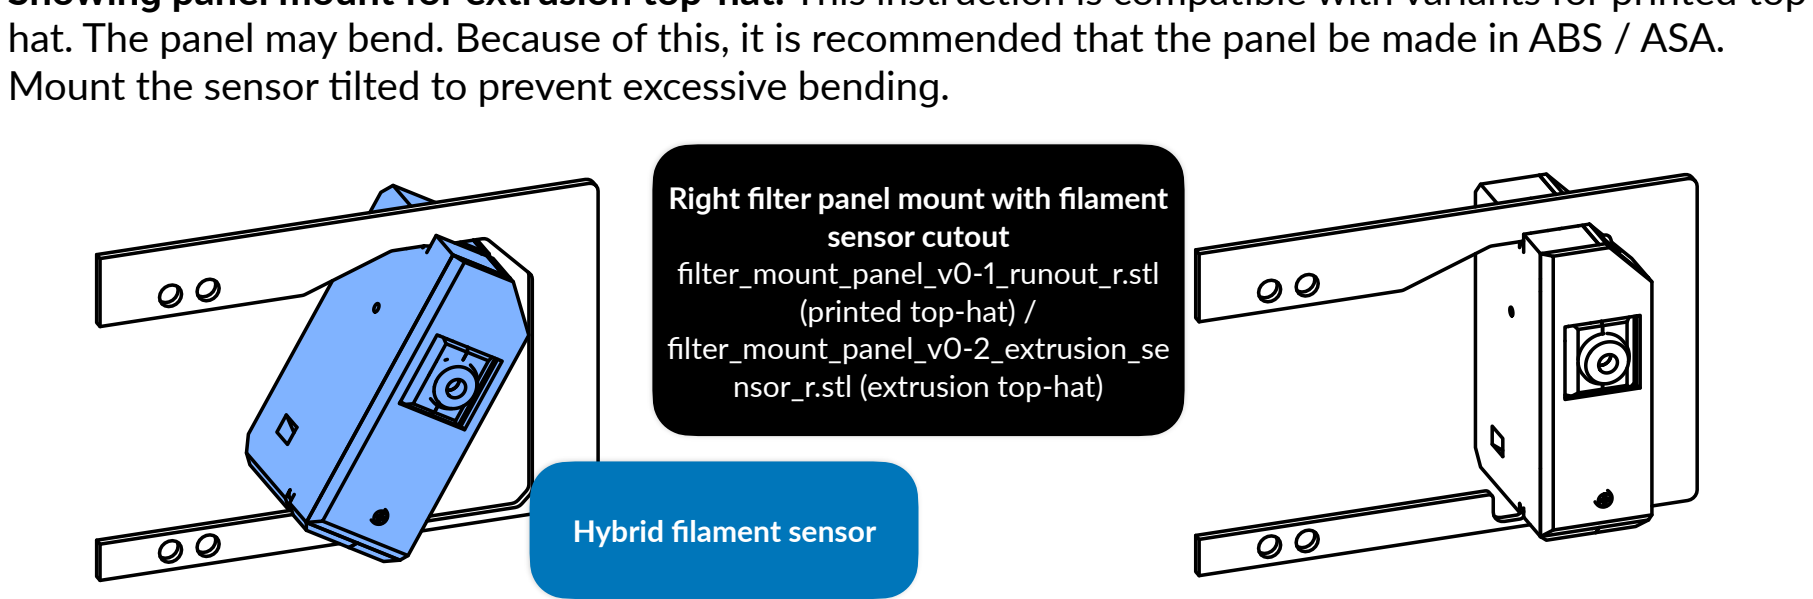
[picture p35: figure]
Hybrid filament sensor; Right filter panel mount with filament sensor cutout filter_mount_panel_v0-1_runout_r.stl (printed top-hat) / filter_mount_panel_v0-2_extrusion_se nsor_r.stl (extrusion top-hat)

hat. The panel may bend. Because of this, it is recommended that the panel be made in ABS / ASA. Mount the sensor tilted to prevent excessive bending.

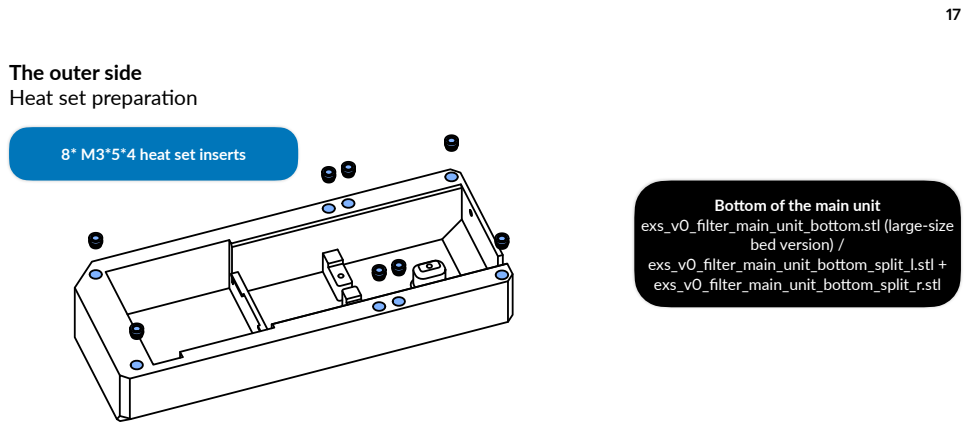
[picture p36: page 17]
bed version) / exs_v0_filter_main_unit_bottom_split_l.stl + exs_v0_filter_main_unit_bottom_split_r.stl

The outer side
Heat set preparation

8* M3*5*4 heat set inserts

Bottom of the main unit

exs_v0_filter_main_unit_bottom.stl (large-size

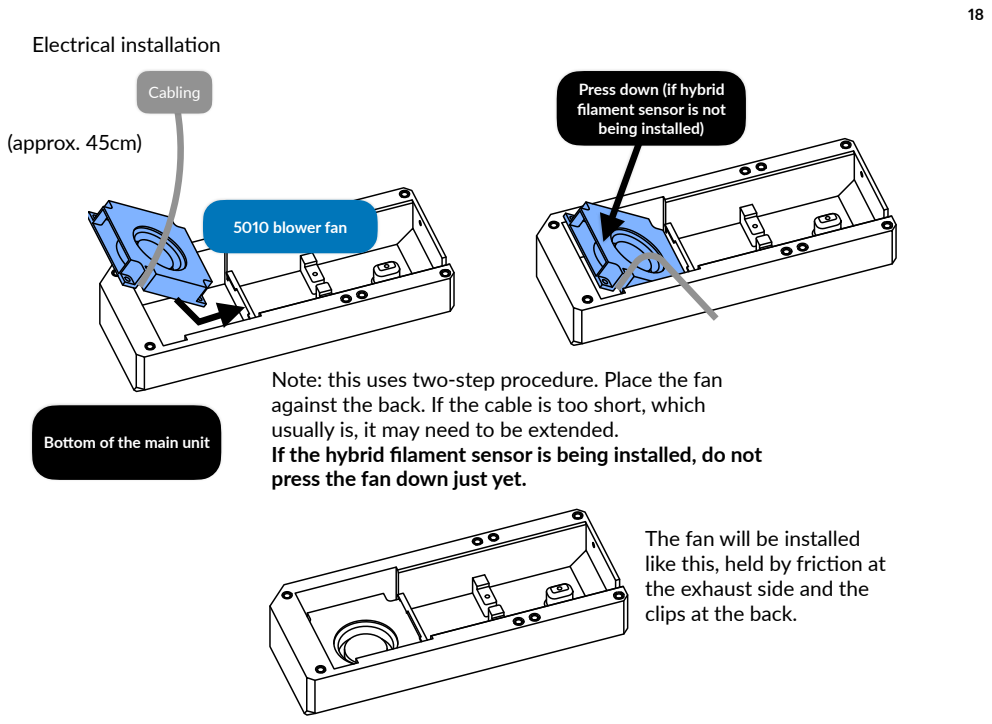
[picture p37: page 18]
Electrical installation; (approx. 45cm); 5010 blower fan; Cabling

Press down (if hybrid
filament sensor is not
being installed)

Note: this uses two-step procedure. Place the fan
against the back. If the cable is too short, which
usually is, it may need to be extended.
If the hybrid filament sensor is being installed, do not
press the fan down just yet.

Bottom of the main unit

The fan will be installed
like this, held by friction at
the exhaust side and the
clips at the back.

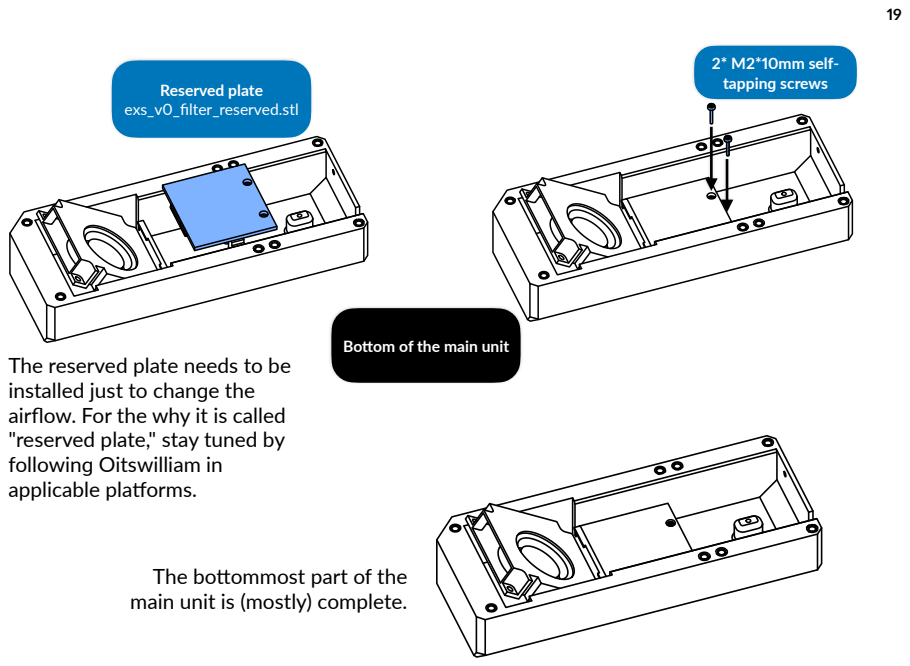
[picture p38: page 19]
Reserved plate exs_v0_filter_reserved.stl; 2* M2*10mm self- tapping screws

Bottom of the main unit

The reserved plate needs to be
installed just to change the
airflow. For the why it is called
"reserved plate," stay tuned by
following Oitswilliam in
applicable platforms.

The bottommost part of the
main unit is (mostly) complete.

20
LED unit
This part is optional.
Preparation - soldering
For BabyDrone Back LED, (https://github.com/Bunny350/BabyDrone-Back-LED) two sets of them are required, and for FPCB LED strip, it should be 4cm (if 100 LEDs per meter) or shorter (if more or less). At the input, the cabling of 24 to 28AWG wires, approximately 450mm per-wire, is then hooked up.

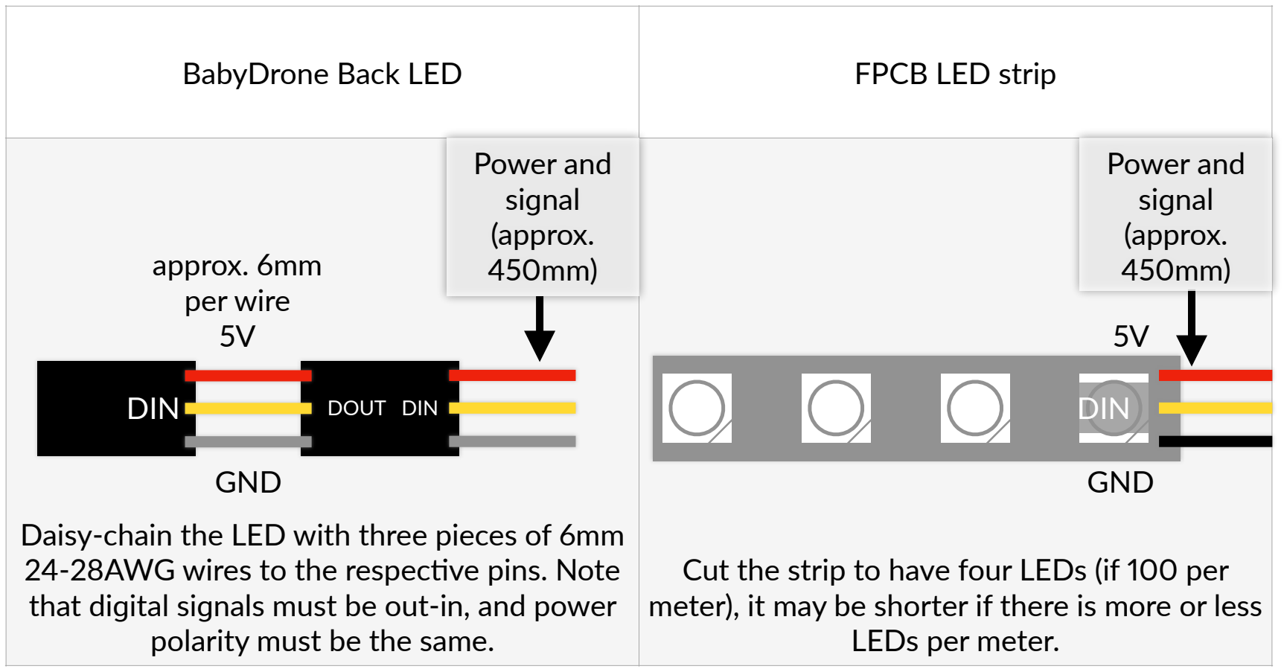
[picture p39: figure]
BabyDrone Back LED; FPCB LED strip; polarity must be the same.; LEDs per meter.; approx. 6mm per wire 5V; DIN; DOUT DIN; GND; Power and signal (approx. 450mm)

Daisy-chain the LED with three pieces of 6mm 24-28AWG wires to the respective pins. Note that digital signals must be out-in, and power

Cut the strip to have four LEDs (if 100 per meter), it may be shorter if there is more or less

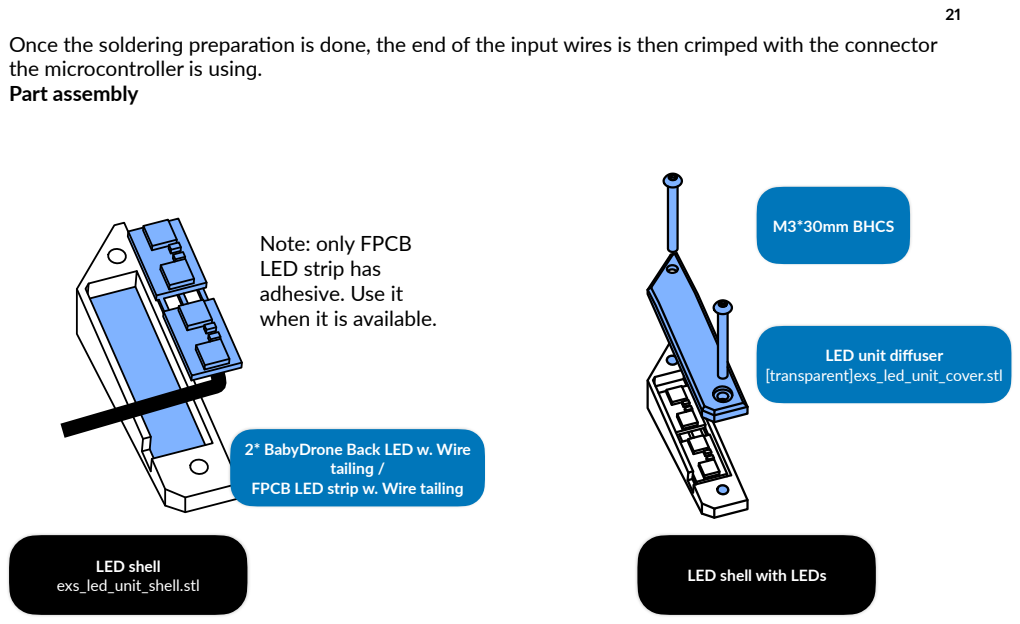
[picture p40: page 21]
tailing /; LED shell; exs_led_unit_shell.stl; LED shell with LEDs; [transparent]exs_led_unit_cover.stl; M3*30mm BHCS

Once the soldering preparation is done, the end of the input wires is then crimped with the connector
the microcontroller is using.
Part assembly

Note: only FPCB
LED strip has
adhesive. Use it
when it is available.

LED unit diffuser

2* BabyDrone Back LED w. Wire

FPCB LED strip w. Wire tailing

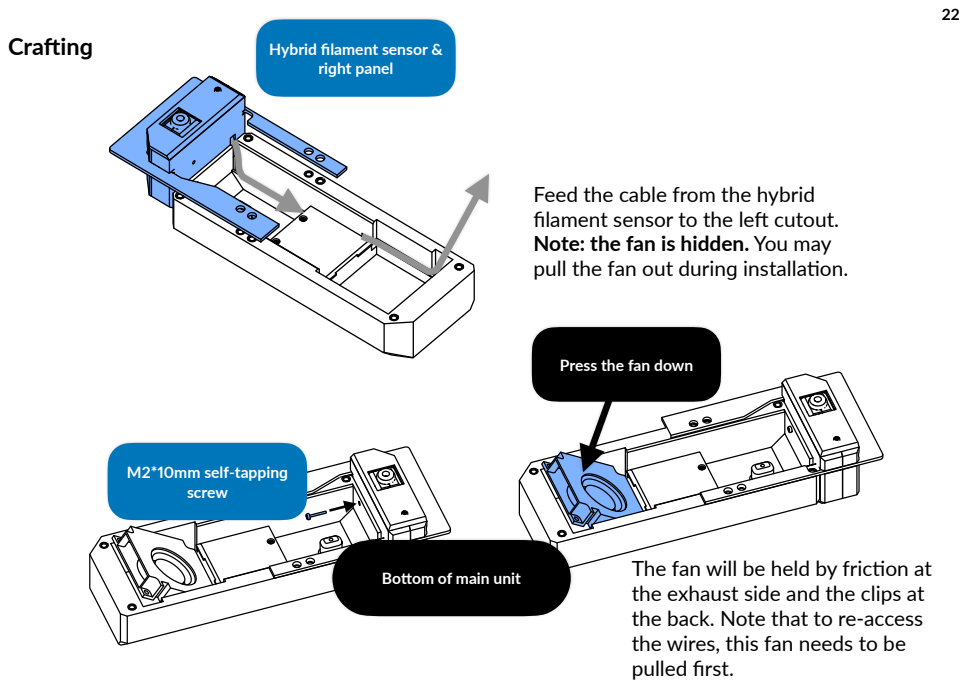
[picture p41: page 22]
Crafting; M2*10mm self-tapping screw

Hybrid filament sensor &
right panel

Feed the cable from the hybrid
filament sensor to the left cutout.
Note: the fan is hidden. You may
pull the fan out during installation.

Press the fan down

The fan will be held by friction at
the exhaust side and the clips at
the back. Note that to re-access
the wires, this fan needs to be
pulled first.

Bottom of main unit

23
Panel mounting

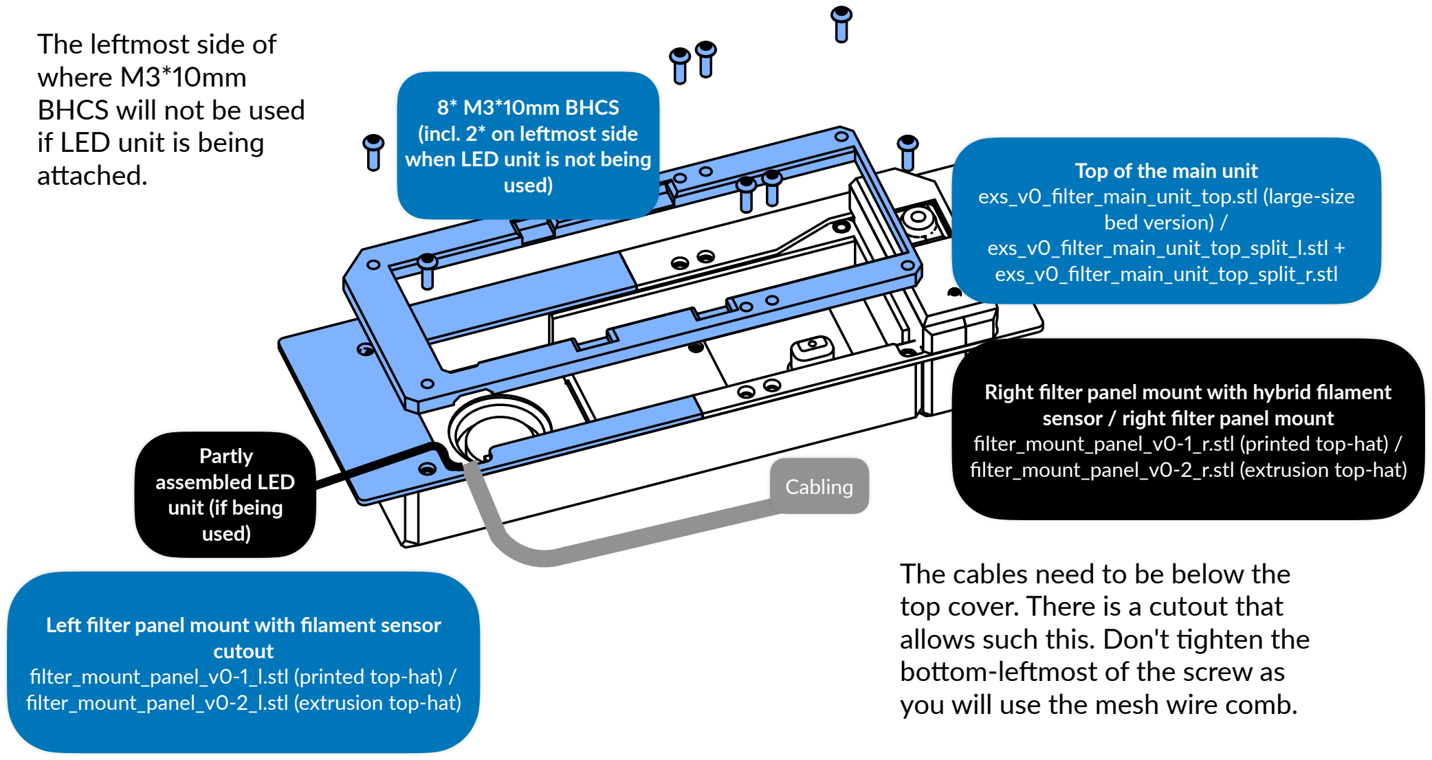
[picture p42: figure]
8* M3*10mm BHCS (incl. 2* on leftmost side when LED unit is not being used); cutout filter_mount_panel_v0-1_l.stl (printed top-hat) / filter_mount_panel_v0-2_l.stl (extrusion top-hat); sensor / right filter panel mount filter_mount_panel_v0-1_r.stl (printed top-hat) / filter_mount_panel_v0-2_r.stl (extrusion top-hat); Top of the main unit exs_v0_filter_main_unit_top.stl (large-size bed version) / exs_v0_filter_main_unit_top_split_l.stl + exs_v0_filter_main_unit_top_split_r.stl; Cabling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

Left filter panel mount with filament sensor

Right filter panel mount with hybrid filament

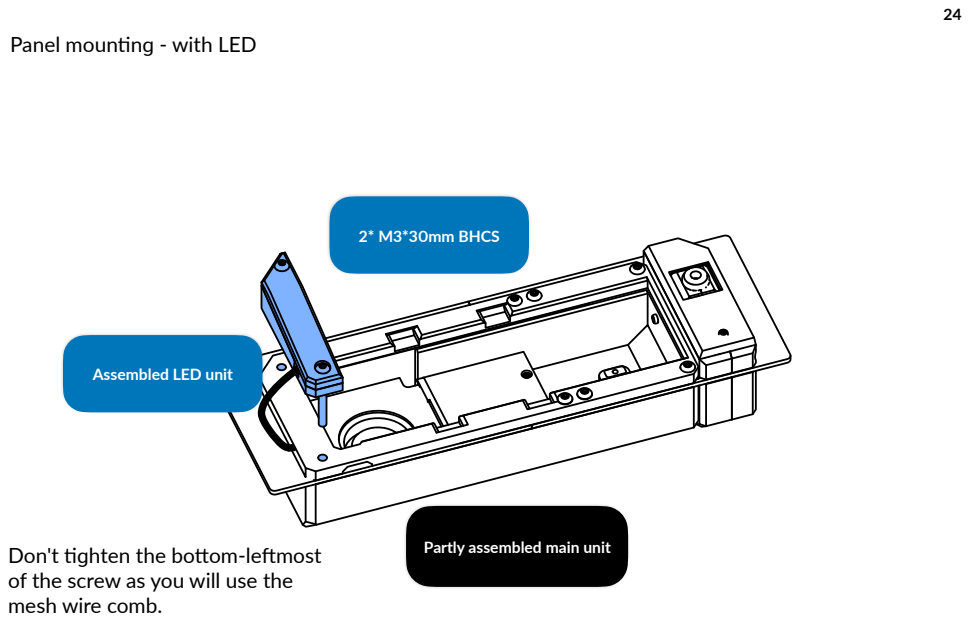
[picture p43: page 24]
2* M3*30mm BHCS

Panel mounting - with LED

Assembled LED unit

Don't tighten the bottom-leftmost
of the screw as you will use the
mesh wire comb.

Partly assembled main unit

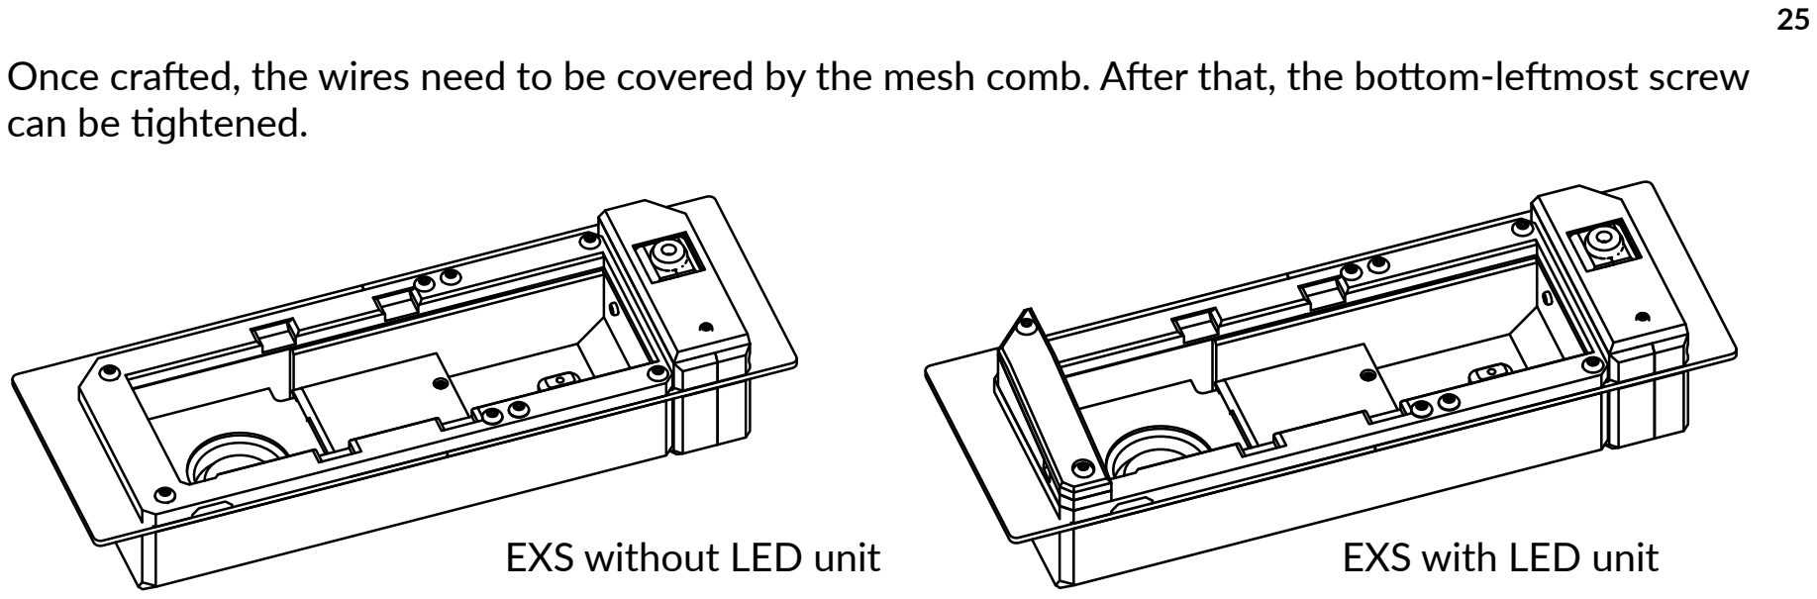
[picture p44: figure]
can be tightened.; EXS without LED unit; EXS with LED unit

Once crafted, the wires need to be covered by the mesh comb. After that, the bottom-leftmost screw

The unit can then be mounted to the back of the printer. This replaces the back top-hat panel of Voron
0. Please refer to page 244 of the original Voron 0.2r1 manual or page 152 of the original Voron 0.1 manual. Note that top-hat from Voron 0.0 is not compatible.

26
Reverse Bowden tube / PTFE tube attaching
To attach, press the tube against the hole of the coupler.
To remove the tube, press the collet of the coupler, and then pull the tube.
There are two couplers in the hybrid filament sensor, pre-sensing and post-sensing sides. Attach the post-sensing PTFE tube where the filament goes to the tool head, and optionally the pre-sensing PTFE tube where it attaches to the compatible dry box.

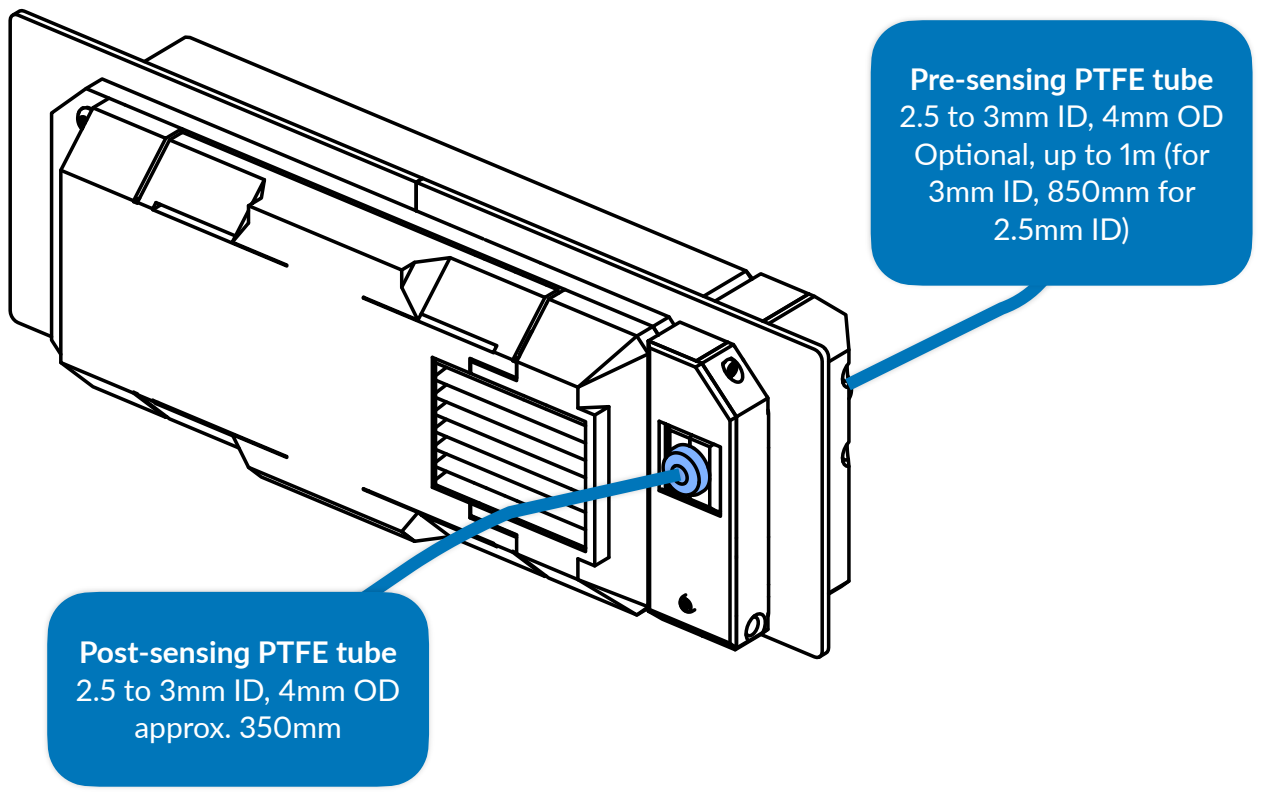
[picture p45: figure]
Post-sensing PTFE tube 2.5 to 3mm ID, 4mm OD approx. 350mm; Pre-sensing PTFE tube 2.5 to 3mm ID, 4mm OD Optional, up to 1m (for 3mm ID, 850mm for 2.5mm ID)

27
Attaching and removal
- To attach the cartridge to the main unit, press the cartridge to the main unit and hear a click.
- To remove the cartridge, squeeze the tabs of the cartridge and then pull it. Don't apply excessive

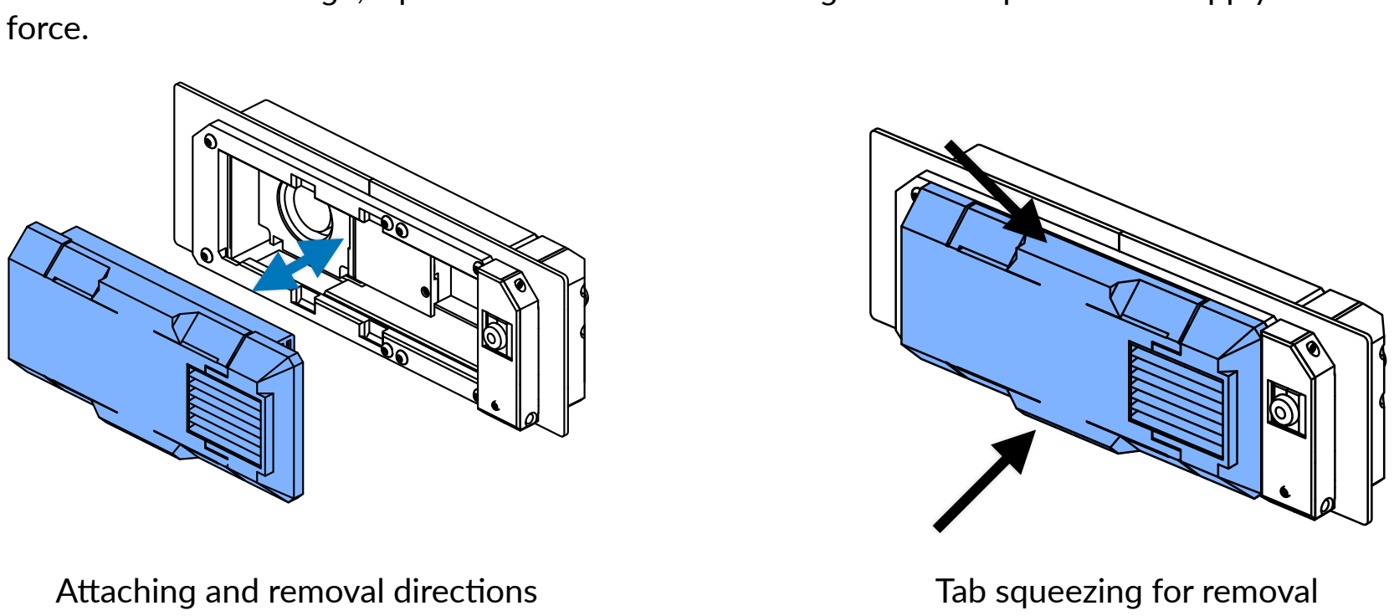
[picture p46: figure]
force.; Attaching and removal directions; Tab squeezing for removal

Activated carbon pellets & front and back HEPA filters replacement
The filters for EXS are easy to be replaced, with minimal to without any tools.
- Remove the cartridge back and back HEPA filter security panels to allow replacement of the back HEPA filter (page 7 for reference),

28
- Remove the cartridge front bracket by pulling it to allow replacement of the front HEPA filter (page 8 for reference).
- Generally, the carbon pellets are recommended to be replaced on every 50 print hours, the front HEPA filter can be replaced on every 360 print hours and the back HEPA filter can be replaced on every 1,080 print hours. Note that the fan overheating is a late indicator of front HEPA filter having captured excessive particles.

Software configuration
The configuration for EXS is very simple unless if the hybrid filament sensor is added.
- The fan in EXS can be connected to the normal fan header of the microcontroller unit (MCU), but the hybrid filament sensor requires two digital signals to be assigned.
- Configuration for BTT Manta M4P demonstrates the connection of FAN2A / 2B (sometimes 3B) as chamber fan and using BL-Touch pins for filament presence and tangle sensing.

29
Troubleshooting
- The tangle sensor keeps triggering even though there are no tangles
- Culprit 1 - the tube before sensing is too long.
- Solution 1 - the tube before pre-sensing must be at least 2.5mm inner diameter and is recommended to be up to 850mm in this inner diameter, or 1 meter for tubes in 3mm inner diameter. Tubes in 2mm or under before the presence sensor is not recommended. Solution 2 may be used if you want to keep the length.
- Solution 2 - if you are using with the multiplexer, or want to keep the original length of the tube, a feed assistant is required and an additional buffer to work around is recommended. It should preload the material when the buffer runs out.
- Culprit 2 - tangle sensor's spring tension is too weak. Change the spring with the coil thickness that meets the spec, such as material of stainless steel and dimensions of 10*25*0.7mm, where 0.7mm is the coil thickness. If the spec spring's coil thickness unfortunately still false-triggers, you can then try using in coil thicknesses 0.1 to 0.3mm thicker. The maximum coil thickness that is allowed is 1mm, which result in total dimensions of 10*25*1mm. Using springs with coil thicknesses too thick may result in stalling the extruder motor instead (when tangle is caught), and 1mm coil thickness can already stall the motors from some of the extruder setups.
- The tangle sensor is not triggering
- Culprit 1 - the material is too soft, it might be TPU / PEBA with shore hardness lower than 95A.
- Solution 1 - bypass the hybrid sensor, this is because the materials that are this soft can lead most extruders stop extruding properly even with low frictions or tubes in high inner diameter.
- Solution 2 - add the feed assistant and buffer, this allows to preload the material and provide friction points opposite to usual.
- Culprit 2 - the lever for the tangle switch is missing. The lever for that switch is required.

30
- Culprit 3 - bad wiring, check the wiring guide, be sure to have heat-shrink tubes with at least three types of color or labels.
- The filter is not filtering properly
- Culprit 1 - the activated carbon pellets has saturated. Replace the carbon pellets by first pulling the cartridge filter panel and then tilt down.
- Culprit 2 - the cartridge is using the non-compliant HEPA filters and / or have no foam around. The recommended filter grade is HEPA13 or over. If there is no 1mm foam around the sides, they should be wrapped around the sides.
- The fan is exhausting way too hot and too ineffectively.
- Culprit - the front HEPA filter has captured excessive particles. Replace the front HEPA filter. This is the late indicator of the front filter having captured excessive particles. Note that brushing the filter or capturing the particles back via vacuum cleaner is ineffective.

31

# Assembly complete

And we are done! If you are satisfied with such product consider tagging @officialbunny350 on Facebook, @oitswilliam on Instagram or @realBunny350 on X (formerly known as Twitter) and share such product with us on Oitswilliam Pang Discord Server.

If you have enquires, problems or issues related to building or using such product, please report it on GitHub.com/Bunny350/OITSWILLIAMV0 and we will get on it.

Change log
- 2026-06-25 - Introduce LED unit for EXS, change Oitswilliam's Instagram handle.
- 2026-06-15 - General availability release. Add the required foam tape around the out side of inner HEPA filter. Change dimensions of the outer HEPA filter. Remove mentions of the upcoming revision of Voron 0 as it wasn't been released yet.
- 2026-04-24 (alpha-ea) - Adjustments, this duplicates incompatibility note on before getting started, add troubleshooting section.
- 2026-04-08 (alpha-ea) - Adjustments, this changes the filter cartridge vectors to have snap-on clips instead of being secured via screws and make the document paper-compliant.
- 2026-03-28-0500 (alpha-ea) - Adjustments, such as fixing words. Add a section about PTFE tubes around the tool head and the pre-sensing. Fix incorrect change log date for the first change.
- 2026-03-28 (alpha-ea) - initial release, make exclusive to the followers of Oitswilliam Pang until June 15.

Manual designed by Oitswilliam Pang. One-person operated design. www.oitswilliam.com

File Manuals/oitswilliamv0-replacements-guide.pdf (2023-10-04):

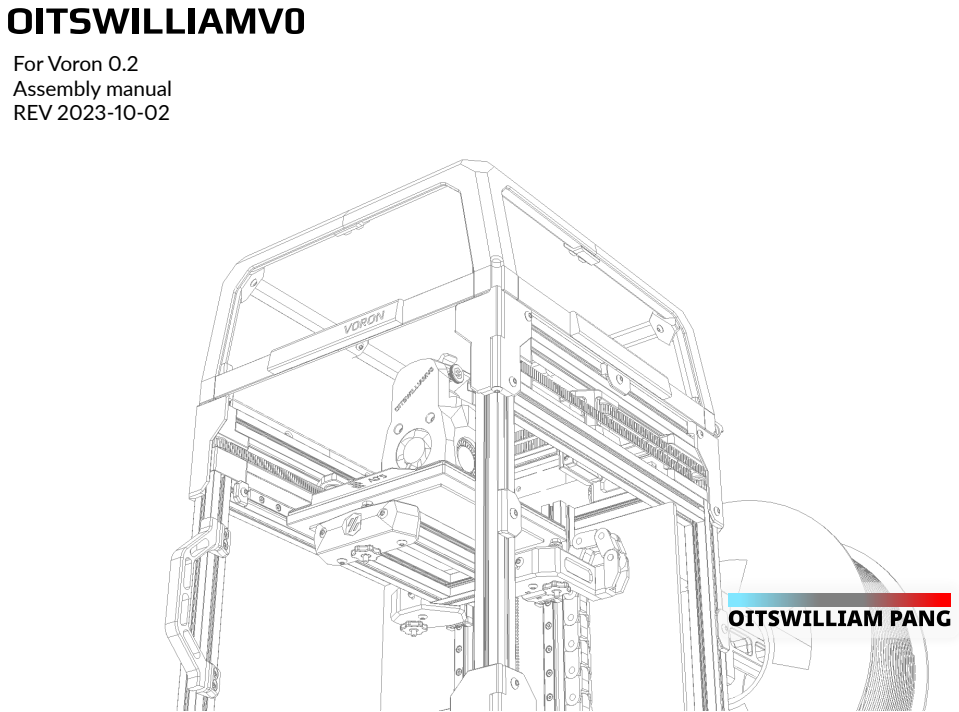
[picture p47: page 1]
For Voron 0.2 Assembly manual REV 2023-10-02

Contents • Before getting started • About OITSWILLIAMV0 • Warnings • Contribution • Support • Part printing • Assembly • Extended skirt • Side skirt USB • As-is top hat • Top hat LED • Display cover • Software configuration • Back skirt fan • Function key

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
# Before getting started

You are about to read the mod project assembly manual.

This manual only shows the replacement parts and not the original parts that aren't modified or is provided by VORON Design.

Extended skirt parts only show the mandatory steps, although will show replacement parts. Other steps can be followed in normal skirt assembly steps from V0.2 assembly guide.

Please read the printer's original assembly manual for the build from start by visiting here. (https://github.com/VoronDesign/Voron-0/tree/Voron0.2/Manuals)

# About OITSWILLIAMV0

OITSWILLIAMV0 is a Voron 0 mod project after OITSWILLIAMV2, a Voron 2 mod project, that redefines mainly on strength and portability, it also has a route which reduces waste.

The original printer design is made by Voron Design with the crew members. Oitswilliam Pang is not one of them.

Extended skirt is a mod that extends the height of Voron 0 skirt which allows you to fit an overpowered Z-axis motor or otherwise things that are currently reserved.

As-is top hat is an extension for V0.1 top hat that adds cam lock and the hinge unit that are introduced in vanilla Voron 0 V0.2. It only requires printing such mod and V0.2 back top panel mount. However it requires your decision of keeping your V0.1 top hat.

Users are allowed to contribute such mod to create an impossible modded 3D printers that will change tinkerers' lives.

# Warnings

Danger: risk of electric shock
- Even though you can build with this mod from start, if you want to wire, or re-wire, you need to make sure and check that the mains is unplugged.
- Failure doing so which is unplugging the mains power may cause electrocution or even death, especially on regions that use 240V.
- When in doubt, please don't touch the wires connected to the power supply or SSR.

# Contribution

Starting in November 2021, every Oitswilliam Pang projects including this will have a dedicated sources and source files for free, which makes them open-source.

If you want to contribute this project, you can visit in GitHub.com/Bunny350.

In other words, each OIWP's projects have their own licensing policies. So if you want to distribute the projects, you need to refer to their licensing policies first.

# Support

Having problems building our projects? You can contact us in Facebook or Twitter. https://www.facebook.com/officialbunny350

However, for the better experience, you can visit and then join Oitswilliam Pang Discord server and receive the community support. Please follow it's rules. https://discord.gg/Cu6e9ra

If you have problems because of the project's errors or simply issues, you can submit them in GitHub. https://GitHub.com/Bunny350/OITSWILLIAMV0/issues

The manual might be updated overtime, so when you start building, or are trying to build the projects, you might need to get the latest manual if it was left for at least every three months.

Thanks for viewing the manual. Now go on the next page to build the first part.

# Part printing

Print guidelines
Each part of the model requires the following set settings, failure to match most of them may result in unexpected damages.
Bold text indicates the recommended value and italic text indicates what setting it is being changed.

Before assembly
To get started building the project, you may use the following tools:
- Soldering iron
- Keystone terminator (if not using Ethernet to Ethernet Keystone jack)
Printer types FDM / FFF or SLS SLA only for parts with no heat-seat parts | Print material: ABS, ASA or PA12 Prohibits PLA. Do not use PETG for motion or enclosing parts.
Layer height of 0.2mm Initial layer height can be 0.2mm or higher | Nozzle and extrusion width must be forced 0.4mm; if using 0.4mm nozzle
1.6mm wall width Or 4 wall counts, excluding tools and jigs | Infill must be at least 40%, excluding tools and jigs
At least 4 solid bottom and top layers. | The best print speed is up to 120mm/s. The speed might be reduced by the hot end flow rate.
Supports are not required. Uncheck generate support if available. | Other settings might be depended on your printer. Follow it's warnings for proper handling.

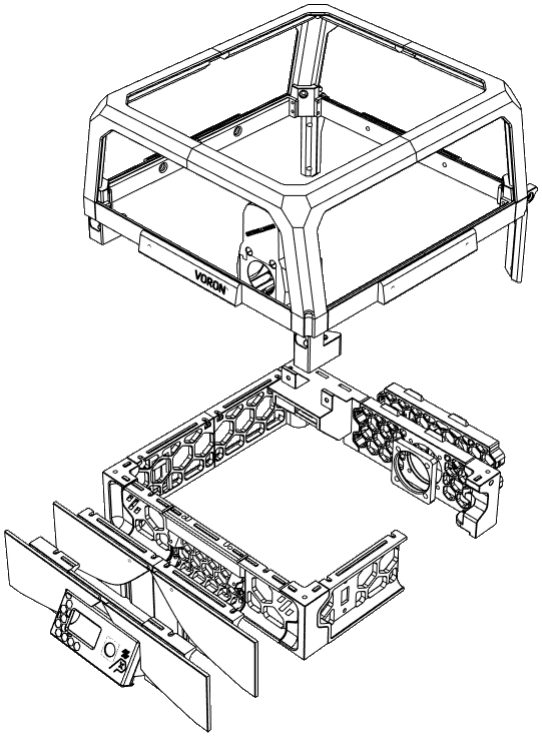
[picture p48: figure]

# Assembly

# Extended skirt

Leggings installation

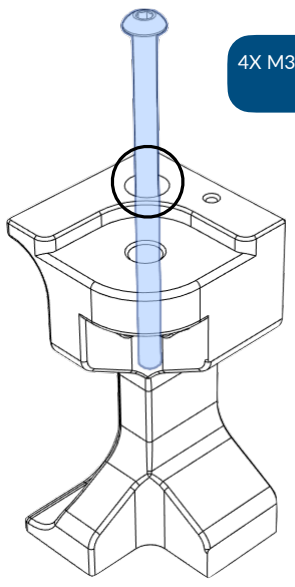
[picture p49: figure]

4X M3x55mm BHCS or
SHCS

Extended skirt legs

To the center tap holes
of bottom side

This step is then
repeated on three
other sides.

Back

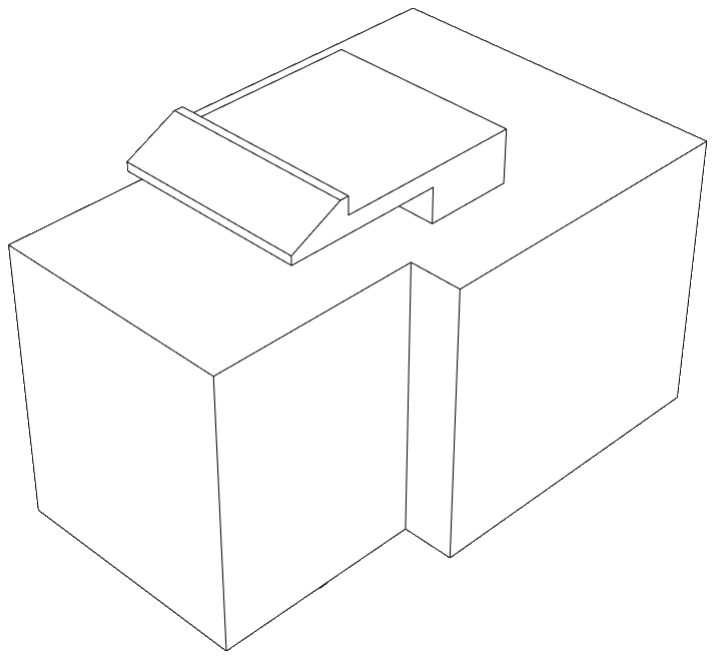
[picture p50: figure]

To insert and wire the Ethernet jack, head to the next page.

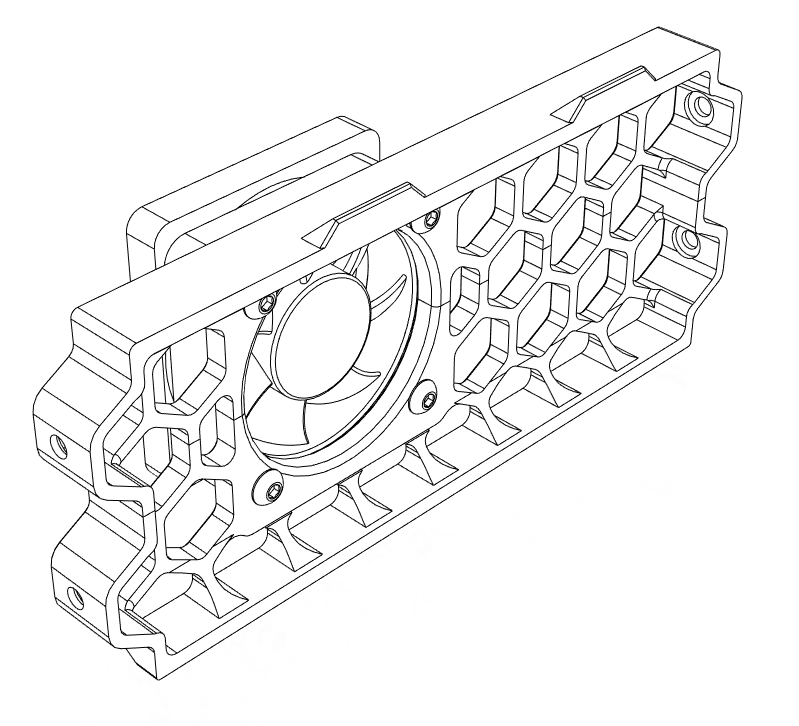
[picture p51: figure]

To install the fan, see or skip to page 12.

Ethernet keystone jack installa

tion

Obtaining the Ethernet cable This mod requires an Ethernet cable of at least 90mm, but the cable must be between 23 to 24 AWG. There are cables which are as thin as in 28 or 30AWG, but they never properly terminate.

CAT6 keystone jacks may not terminate with CAT5 cables, although CAT5 keystone jacks can terminate with CAT6 cables.

This slot does not support AMP keystone jacks, due to it being too wide.

4X M3x6mm
BHCS

Back skirt halves

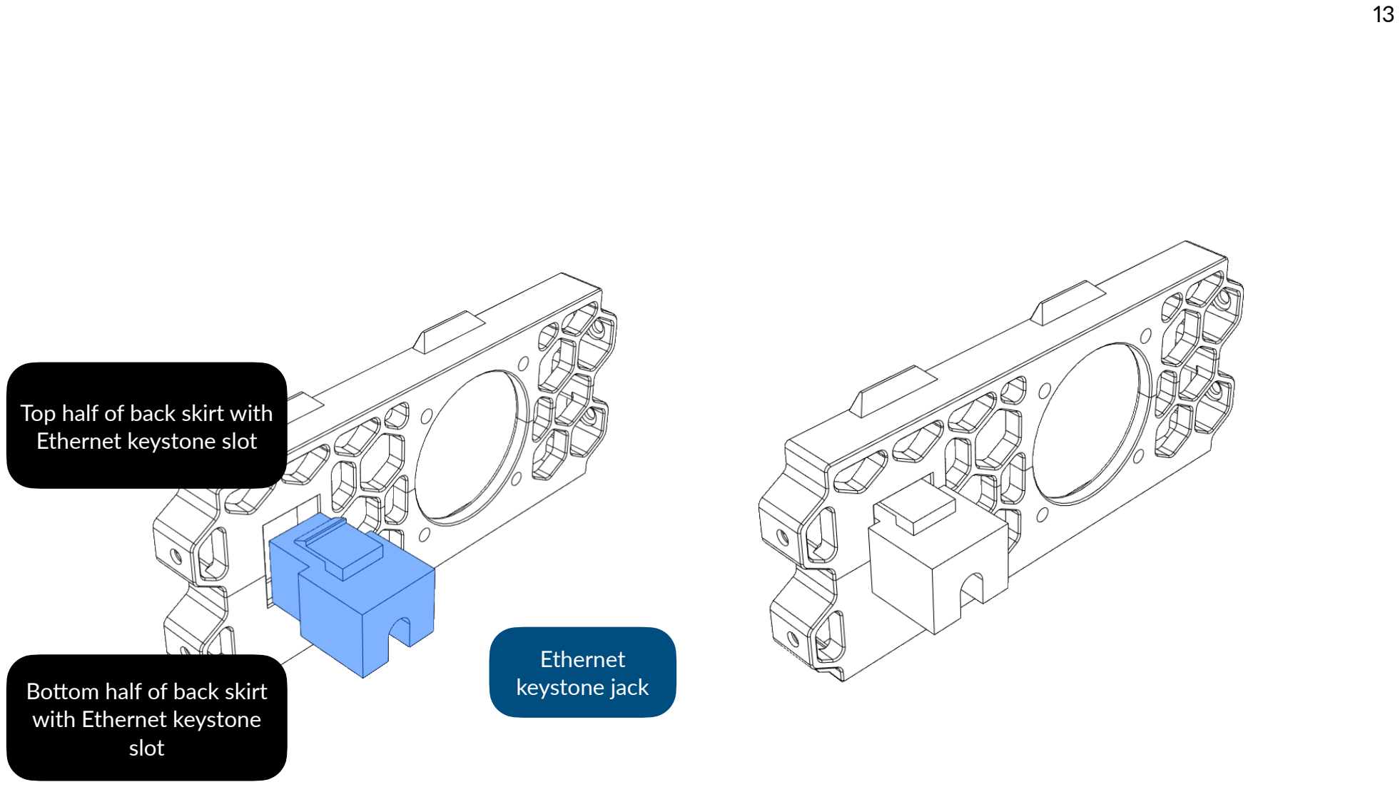
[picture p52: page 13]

Ethernet
keystone jack

Top half of back skirt with Ethernet keystone slot

Bottom half of back skirt
with Ethernet keystone
slot

Back skirt fan installation
You may need to turn the printer away from being right-side up to ease the process. This shows right-side up.
Preparation

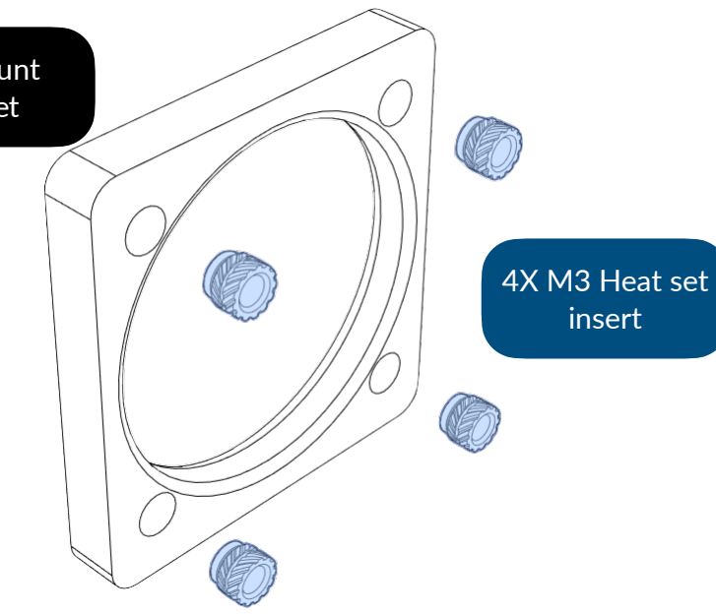
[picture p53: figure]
4X M3 Heat set insert
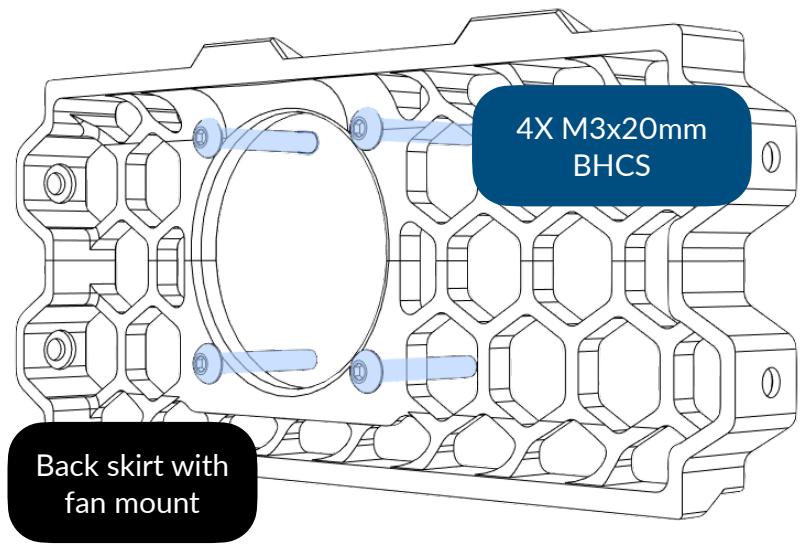
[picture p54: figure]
4X M3x20mm BHCS; Back skirt with fan mount

Fan mount
bracket

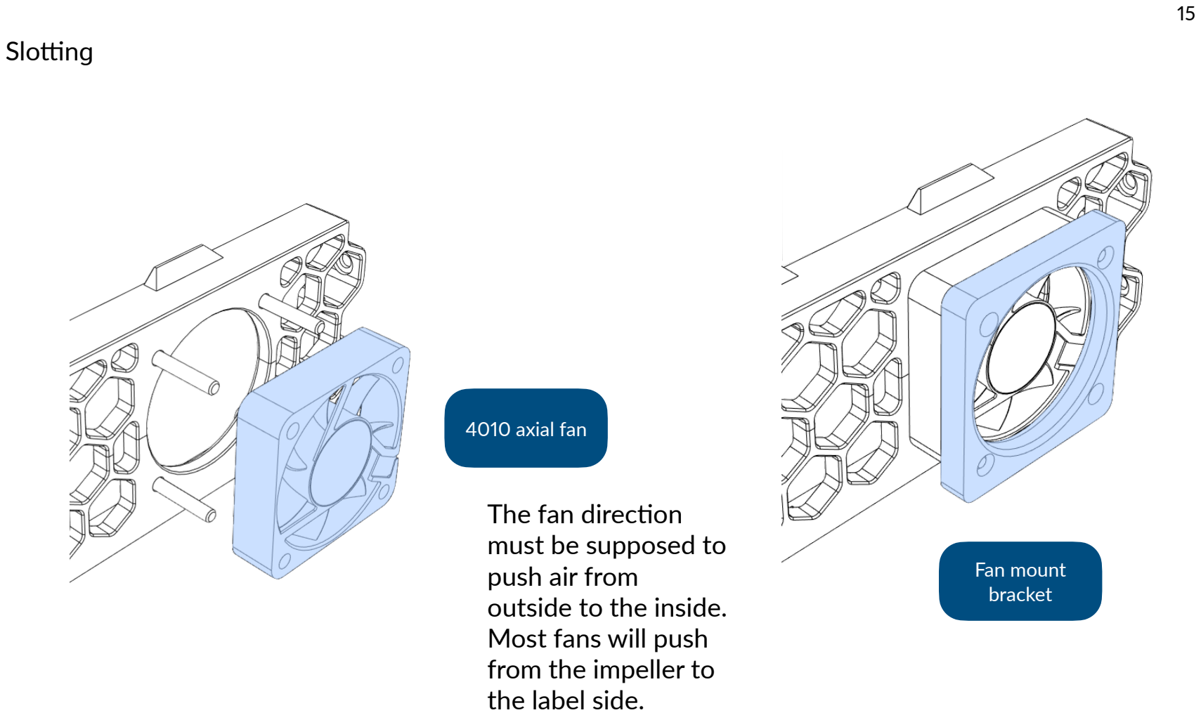
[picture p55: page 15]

Slotting

4010 axial fan

Fan mount
bracket

The fan direction
must be supposed to
push air from
outside to the inside.
Most fans will push
from the impeller to
the label side.

After slotting the axial fan and the mounting bracket, you have to do the cross-pattern when tightening the fan mount screws (4X M3x20mm). This pattern makes

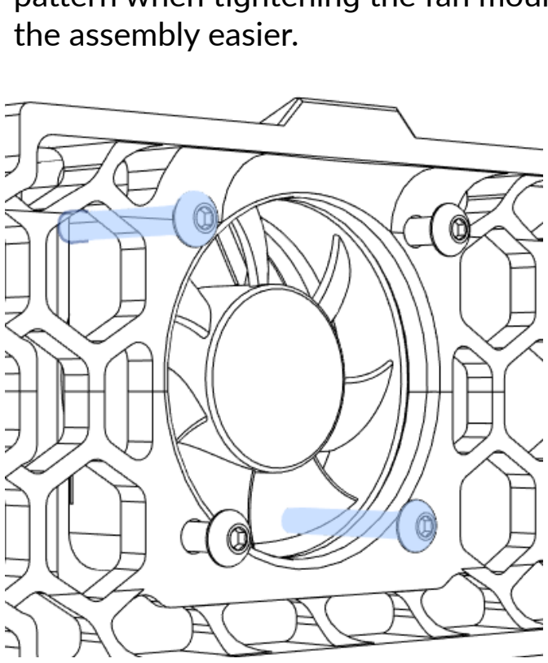
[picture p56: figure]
the assembly easier.
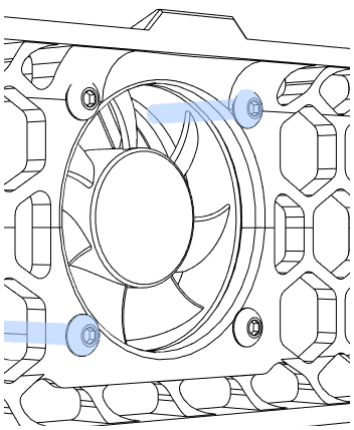
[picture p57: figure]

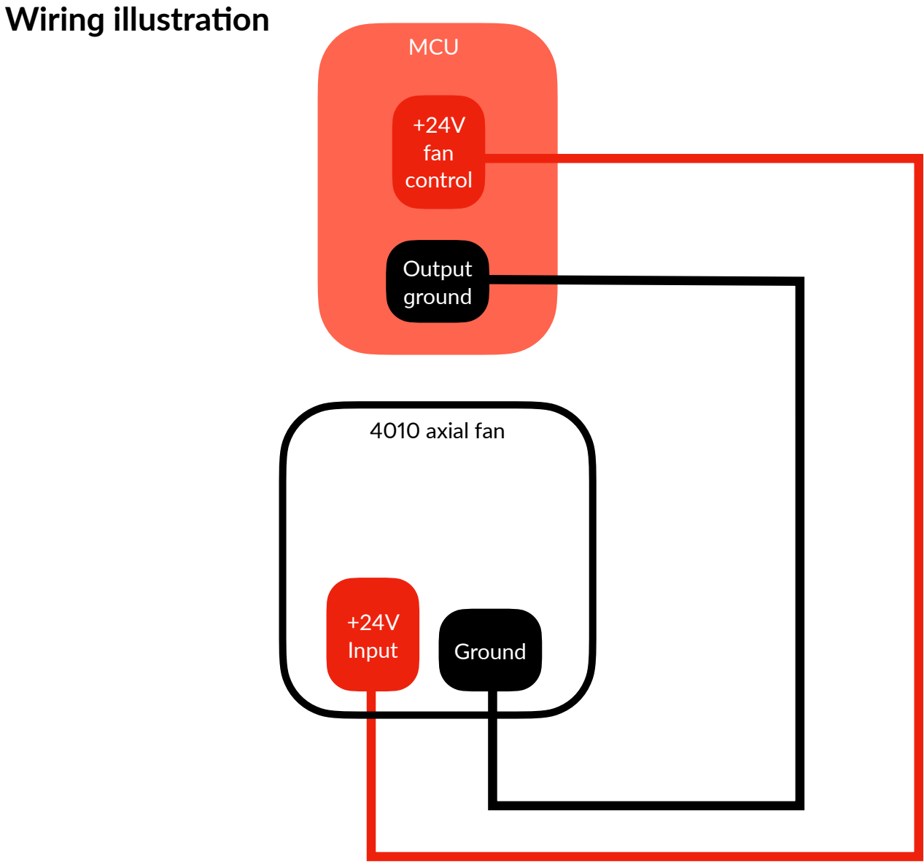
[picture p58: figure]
Wiring illustration; MCU; 4010 axial fan; Ground; +24V Input; Output ground; +24V fan control

# Side skirt USB

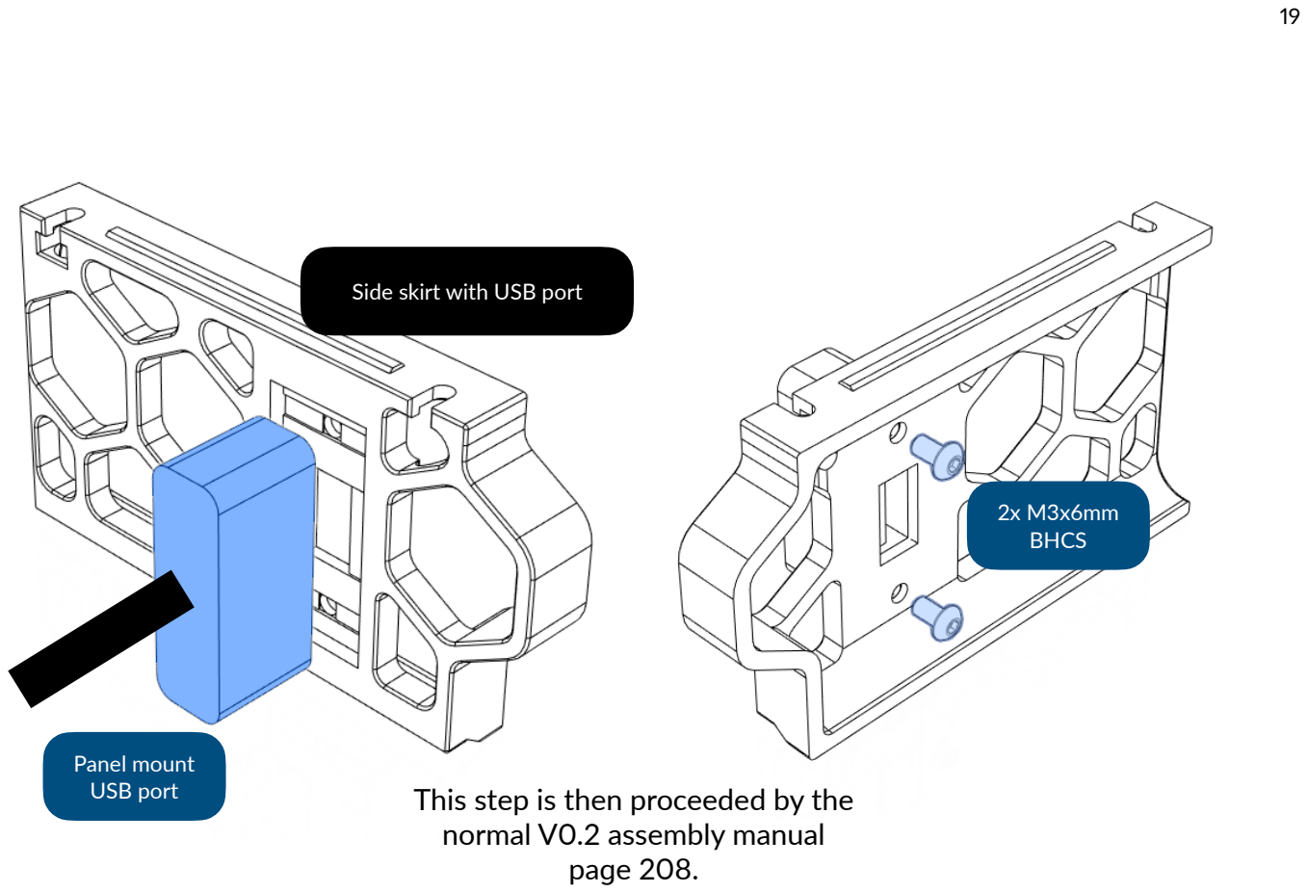
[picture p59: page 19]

Panel mount
USB port

2x M3x6mm
BHCS

Side skirt with USB port

This step is then proceeded by the normal V0.2 assembly manual page 208.

# As-is top hat

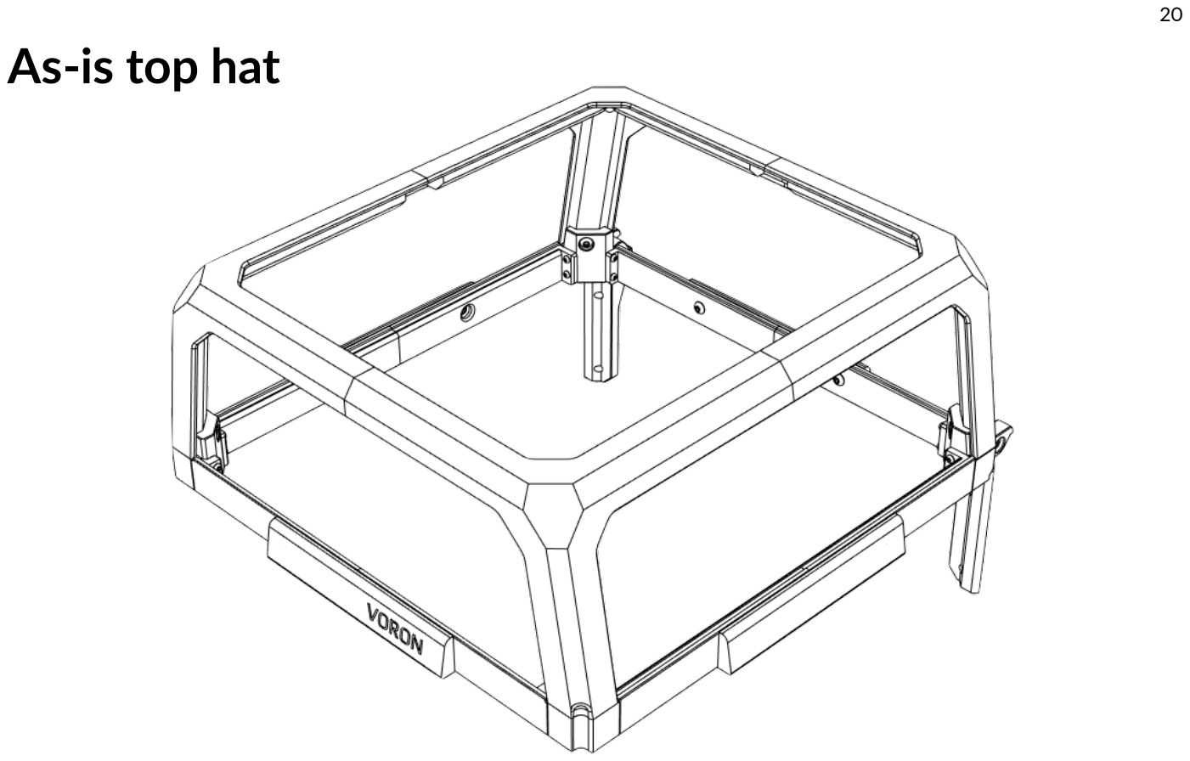
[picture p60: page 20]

Halo / Ring assembly

These corners and spacing brackets are side-dependent. Please check their alignments before tightening.

Back side: thin, no chamfered edges. | Left and right sides: thicker than for back side, has chamfered edges

Front side: thin, has flush endings and chamfered edges

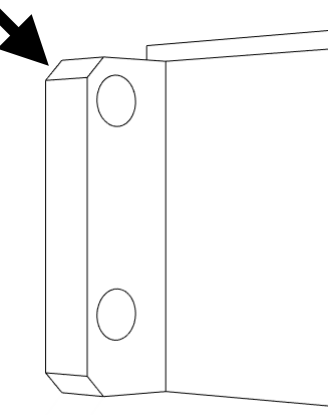
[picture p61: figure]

4x (2x per side) M2x10mm
Self-tapping screws

Half of side spacing bracket

Back left top hat corner

Half of back spacing bracket

You may repeat on the right hand side.

4x (2x per side) M2x10mm
Self-tapping screws

Half of side spacing bracket

Front right top hat corner

Half of front spacing bracket

You may repeat on the left hand side.

Front left quarter

Front right quarter

Back left quarter

Back right quarter

Spacer holding bracket | Spacer holding bracket

Spacer holding bracket

Spacer holding bracket

8x M3x6mm BHCS
(2x per side)

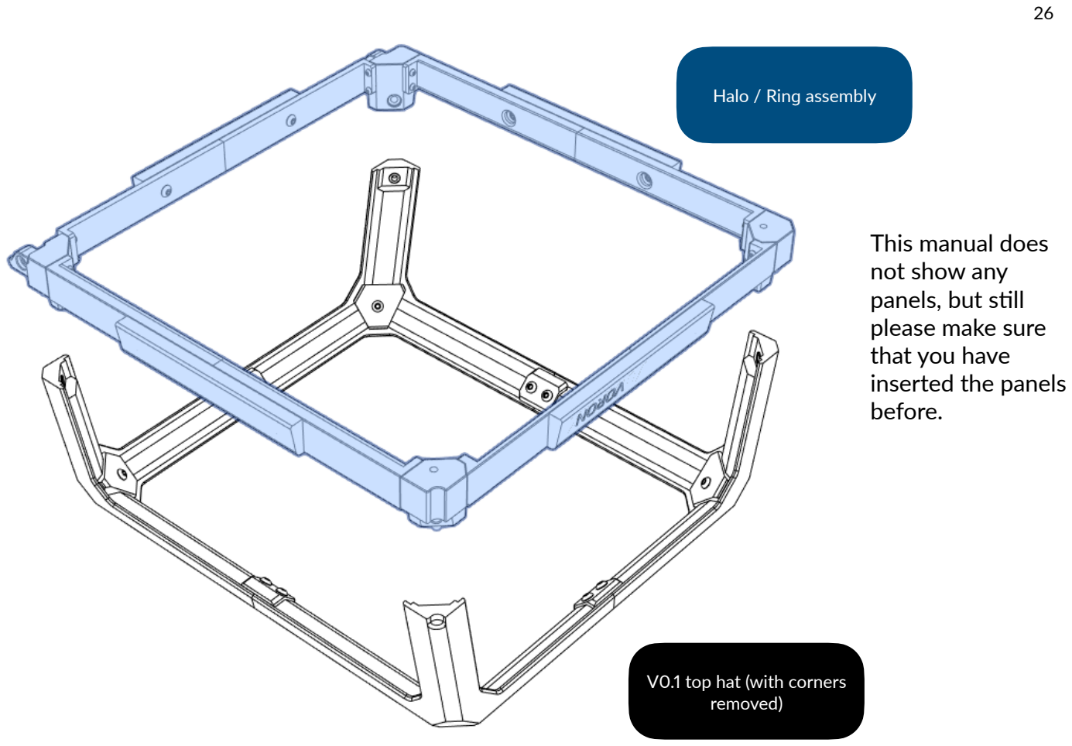
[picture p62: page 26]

V0.1 top hat (with corners removed)

Halo / Ring assembly

This manual does
not show any
panels, but still
please make sure
that you have
inserted the panels
before.

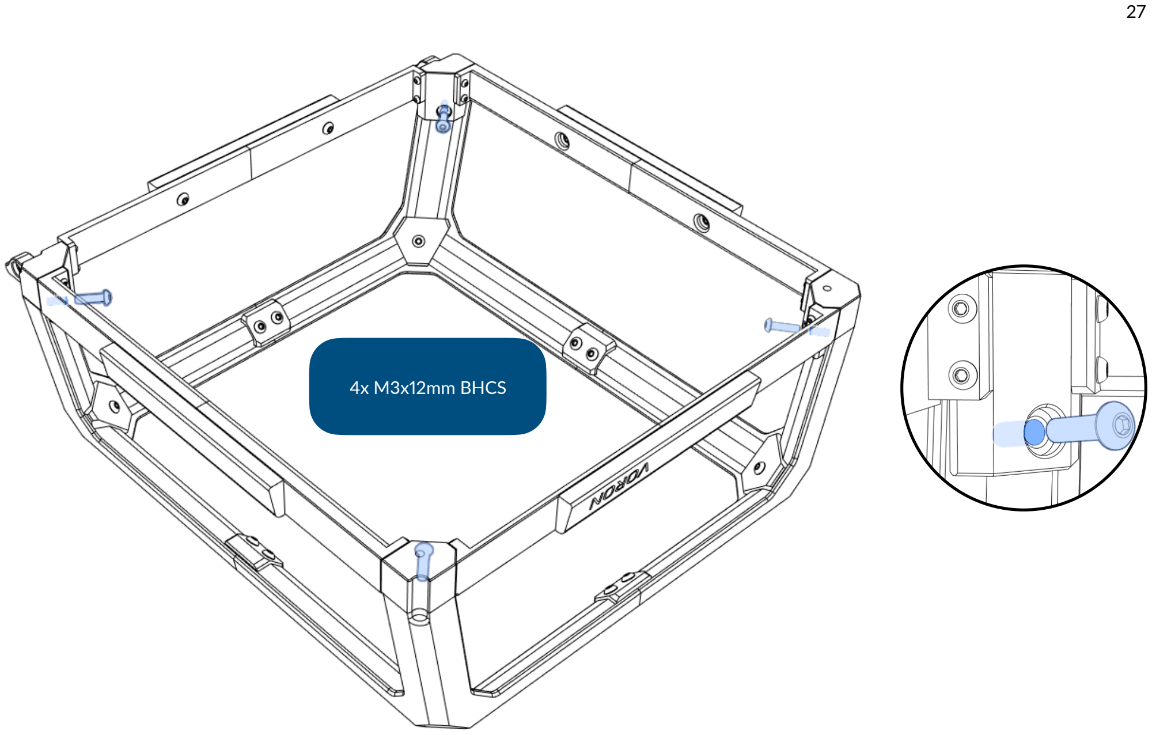
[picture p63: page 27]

4x M3x12mm BHCS


Cam lock slot mounting

Front corners

M3x10mm BHCS

This step is then followed by the normal V0.2r1 assembly manual page 246.

You may use the pulley jig from original parts to make sure that the notch screw locking the top hat has the proper height.

4x M3x10mm BHCS

About 5mm spacing

# Top hat LED


Wiring

Inside the unit; LED 1; LED 2; GND; DOUT; DIN; To the MCU; (approx. 16mm); (approx. 600mm)

Building LED unit

Please make sure it has no or minimal seams. If the magnet is not secure, you may use RTV silicone or superglue to stick the magnets with the part.

Back of LED unit

MCU

MCU

Upside down view.


4x M2x10mm self-tapping screws

LED unit diffuser


Mounting to the frame

2x 6x3mm magnets

This time we have to attract another magnets to ease assembly.

LED unit mount

Note: if the holes are too big, you may need to do the traditional method by sticking magnets with RTV silicone or superglue. The attracting side must face outside.


For V0.1 top hat, you can keep M3 screws to secure the mount. No hex nuts are required.

For V0.2 extruded top hat, you need to disassemble the top-front part of top hat and then load 2 M3 nuts and prepare M3*8 screws.

V0.1 top hat | V0.2 extruded top hat

LED unit

2x M3 hex nut

Top-front part of
extrusion J

They should be
inside facing back.

2x M3x8mm BHCS

# Display cover


This is an add-on for V0.2 display that adds additional protections.

Side display cover

Front display cover

This is then secured with 4x M2x10mm screws and then
followed by the third part of page 219 on the normal V0.2r1
assembly manual.

# Software configuration

Back skirt fan
This fan needs to be manually assigned in order to run. This code will be put into configuration folder. This fan is recommended to be assigned as controller cooling fan.

Top hat LED
This feature adds the ability to add glow that is direct to the front side of the model allowing you to see with minimal light. This code will allow you to do that.

Add new controller fan
Fan pin to be assigned (you need to change to pin assigned to)
Idle timeout (in seconds)
Associated heater pin (set to bed heater)

Add new LED called top_hat_led
Pin to be assigned
Chain count (add one per LED)
Color order (not required if using defaults) Emission value on startup

Function key
This feature replaces emergency stop key found in V0 displays. It replaces with multiple functions depending on the printer's situation. When the printer is idle, pressing the function key or previously known emergency button will initialize homing, during printing, pressing it will pause the print. Pressing it again will resume print. You may go to fn_key.cfg (https://github.com/Bunny350/OITSWILLIAMV0/tree/For-V0.2/Firmware/fn_key.cfg) for more information.

# Assembly complete

Now you can share the mod with any one of us or them, in the near future we will unlock the superpowers of unusual usage of such printer. However this manual does not include unusual guides and troubleshooting guides. This means, if you have problems with this mod, you need to head to https://github.com/Bunny350/OITSWILLIAMV0/issues, join and message in Oitswilliam Pang Discord server or message @officialbunny350 on Facebook.

It's done. While you are at my social platforms maybe should you follow me?

Manual designed by Oitswilliam Pang. One-person operated design. bunny350.github.io

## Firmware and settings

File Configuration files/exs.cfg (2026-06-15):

## This file contains mappings and features that are used in
## Exhaust XS for Voron0. To assign this file to your config,
## you can add [include exs.cfg] in your base config (printer.cfg)
## file.

## This is made for BTT Manta M4P V2 by-default. You may need
## to change the pins before applying changes, if there are
## pinout differences between BTT Manta M4P and your 
## microcontroller unit board.

## Note: for BTT Manta M4P, we have to use the BL-Touch
## port as filament sensor.

[filament_switch_sensor presence]
switch_pin: ^!PC14 # Switch is connected normally-open.
pause_on_runout: False # this feature only checks for printing state but it covered busy states
runout_gcode:
    {% if (printer.print_stats.state == 'printing') and (printer.print_stats.filename is not none) %}
        PAUSE # [pause_resume] is required in printer.cfg
        RESPOND TYPE=echo MSG='Filament ran-out, please refill (or change) the filament.'
        M117 Filament runout
    {% endif %}
insert_gcode:
    {% if (printer.display_status.message == 'Filament runout') %}
        M117
    {% endif %}

[filament_switch_sensor tangle]
switch_pin: ^!PA1 # Switch is connected normally-closed, but still must have state inverted.
pause_on_runout: False
runout_gcode:
    {% if (printer.print_stats.state == 'printing') and (printer.print_stats.filename is not none) %}
        PAUSE # [pause_resume] is required in printer.cfg
        RESPOND TYPE=echo MSG='Filament tangle detected, please check the filament tangle and address it.'
        M117 Filament tangled
    {% endif %}
insert_gcode:
    {% if (printer.display_status.message == 'Filament tangled') %}
        M117
    {% endif %}

## Exhaust fan
## NOTE: This config might exist in your printer config file before
## EXS was installed. If the printer config file contains an exhaust
## fan section, you may comment this section.
[heater_fan exhaust_fan]
pin: PD4 # PD4 being FAN2 (A and B, or sometimes 3B) in BTT Manta M4P.
fan_speed: 1.0
max_power: 1.0
# shutdown_speed: 0.4
kick_start_time: 5.0
heater: heater_bed
heater_temp: 60

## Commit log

2023-01-08 Final release
    Will skip to for V0.2
    [[a]foot-front-left-extended.stl, [a]foot-rear-left-extended.stl, [a]rear-foot-right-extended.stl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]
2023-01-09 WIP branch
    Publishing it as WIP branch until when prototypes work
    Don't work at or beyond 1AM it made me look bad at typing
    [[a]foot-front-left-extended.stl, [a]foot-rear-left-extended.stl, [a]rear-foot-right-extended.stl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]
2023-02-04 Parts for V0.2 release
    [MiniSB-Cowling-OITSWILLIAMV0-SE.stl, [rc]rosalinatheme-decal-cover-righthand.stl, [rc]rosalinatheme-decal-cover.stl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]
2023-02-14 Add As-is top hat for upgrading V0.1 to V0.2
    [corner-front-left.stl, corner-front-right.stl, corner-hinge-left.stl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]
2023-02-22 Compatibility and critical design error fix
    This change fixes critical part error that prevents a screw from being inserted.
    It adds a simple yet complicated assembly guide for as-is top hat mod.
    This also change the back skirts to make them printable in limited volume, change on side spacing covers for simplification and updated repo introduction
    [back-skirt-bottom.stl, back-skirt-ethernet-bottom.stl, back-skirt-ethernet-fan-bottom.stl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]
2023-03-06 As-is top hat changes
    * Side hole adjustments on corners
    * Remove normal side spacing brackets, while thick and ultra-thick versions remain
    * Minor change to spacing brackets
    [corner-front-left.stl, corner-front-right.stl, corner-hinge-left.stl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]
2023-03-08 (Back corners) Minor orientation change
    [corner-hinge-left.stl, corner-hinge-right.stl]
2023-03-23 Leg screw mount offset and brim chamfer fix
    This change only change leg mounting screw depth and brim chamfer fix in USB port side skirt.
    [[rc]rosalinatheme-decal-cover-righthand.stl, [rc]rosalinatheme-decal-cover.stl, front-foot-extended-lefthand.stl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]
2023-05-13 Add new mods and changes
    This update adds non-printable hardware and to CAD and adds new mods such as top hat LED, display side cover and face plate with function key. It also fix some inconsistencies compared to original un-modded parts
    [[a]_skirt_logo_x2.stl, [acc]v0-led-top-hat-clip.stl, [rc]rosalinatheme-decal-cover-with-display-mirror.stl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]
2023-10-04 Assembly manual and minor changes
    This change adds assembly manual and the following changes:
    * Move display cover to it's own folder
    * Add display cover with USB cutout
    * Update CAD files
    This also known as Phase 1 finale so stay tuned for a new major additions
    [display-cover-usb.stl, display-cover.stl, v0 led addon v3.f3d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]
2023-10-08 Update render of phase 1 and add a feature printer
2025-10-10 Update config.yml
    Sudden screw up but I bet I have low hopes of mailto and issue integration
2026-04-11 Update headless-front-extended.stl to base of Trident
    This update changes headless-front-extended.stl to have bigger pattern just to make it consistent with the front-sides of the skirt panels.
    [OITSWILIAMV0 P1 V0.2.f3d, OITSWILIAMV0 V0.2.f3d, headless-front-extended.stl]
2026-04-11 Update headless-front-extended.stl to base of Trident
    This update also adjusts Readme file.
    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
    [OITSWILIAMV0 P1 V0.2.f3d, OITSWILIAMV0 V0.2.f3d, headless-front-extended.stl]
2026-04-21 Rename "Firmware" folder to configuration files
    This also adds the Readme document about the folder.
    [fn_key.cfg]
2026-06-15 Exhaust XS officially released
    This change introduces Exhaust XS and CAD assembly of it (that even followers had no access, they only access STL models).
    Please note that the LED mount is not included as STLs as there is no manual for it (only CAD models). Essentially such requires the leftmost M3x10s to be replaced with M3x30.
    [EXS for voron 0.f3d, EXS for voron 0.step, exs.cfg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]
2026-06-25 [EXS] Introduce LED unit
    This update adds printable files of LED unit for Exhaust XS as an optional extension, it was only included in CAD as that was not done previously. This also updates the manual to include the LED unit.
    LED unit requires either LED strip of up to 4cm or two sets of OIWP BabyDrone Back LED https://github.com/Bunny350/BabyDrone-Back-LED .
    [[transparent]exs_led_unit_cover.stl, exs_led_unit_shell.stl]
2026-06-26 Re-orient printable models
    [[transparent]exs_led_unit_cover.stl, exs_led_unit_shell.stl, exs_presence_tangle_pres_l.stl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]
